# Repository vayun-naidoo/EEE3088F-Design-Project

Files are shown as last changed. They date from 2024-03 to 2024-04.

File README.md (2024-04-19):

**EEE3088F MICRO MOUSE DESIGN PROJECT**  
The project requires the construction of two submodules that interface with a micromouse robot. The robot is designed to complete a maze after finding the most optimal path to traverse.
The two submodules are for the **power** and **sensing** requirements of the micromouse. All design schematics and datasheets considered can be found in this repository.  

**POWER**  
The power submodule is required to distrubute the power from a 1S1P battery to the motors on the micromouse as well as power the other submodules such as the processor and the sensing apparatus. 
THe system is also required to monitor the battery's state of charge (SoC) through the processor's ADC.

**SENSING**  
The sensing subsystem is required to, at close range(+-5cm) produce a voltage to the micro controller. This voltage must be distinguishable from a further range output(+10cm). It is also required to not drain the battery of the micro mouse as it needs to traverse a maze for roughly 10 minutes.

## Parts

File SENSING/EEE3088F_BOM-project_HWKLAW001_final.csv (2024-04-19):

Comment | Designator | Footprint | LCSC
NPN | Q9 | SOT-23 | C139719
100 | R2 | R_0805_2012Metric | C17408
10k | R17,R20,R8 | R_0805_2012Metric | C17414
150 | R3 | R_0805_2012Metric | C17471
1k | R19,R22,R31 | R_0805_2012Metric | C17513
20 | R1,R10,R11,R12,R13,R14,R15,R5,R6,R7,R9 | R_0805_2012Metric | C17544
51 | R23 | R_0805_2012Metric | C17738
5k | R16,R18,R21,R24,R4 | R_0805_2012Metric | C27834
D_Photo | D2,D7,D8 | LED_D5.0mm_Horizontal_O1.27mm_Z3.0mm_IRBlack | C2900211
LD271 | D1,D10,D3,D4,D5,D6 | LED_SideEmitter_Rectangular_W4.5mm_H1.6mm | C57092
SJ_OPEN | JP17 | SolderJumper-2_P1.3mm_Open_RoundedPad1.0x1.5mm
SJ_OPEN | JP2 | SolderJumper-2_P1.3mm_Open_RoundedPad1.0x1.5mm
SJ_OPEN | JP5 | SolderJumper-2_P1.3mm_Open_RoundedPad1.0x1.5mm
SJ_OPEN | JP10 | SolderJumper-2_P1.3mm_Open_RoundedPad1.0x1.5mm
SJ_OPEN | JP6 | SolderJumper-2_P1.3mm_Open_RoundedPad1.0x1.5mm
SJ_OPEN | JP7 | SolderJumper-2_P1.3mm_Open_RoundedPad1.0x1.5mm
TestPoint | TP1 | TestPoint_Pad_1.5x1.5mm
TestPoint | TP4 | TestPoint_Pad_1.5x1.5mm
SJ_OPEN | JP16 | SolderJumper-2_P1.3mm_Open_RoundedPad1.0x1.5mm
SJ_OPEN | JP8 | SolderJumper-2_P1.3mm_Open_RoundedPad1.0x1.5mm
SJ_OPEN | JP9 | SolderJumper-2_P1.3mm_Open_RoundedPad1.0x1.5mm
Conn_01x28_Pin | J1 | PinSocket_2x14_P2.54mm_Vertical
SJ_OPEN | JP3 | SolderJumper-2_P1.3mm_Open_RoundedPad1.0x1.5mm
SJ_OPEN | JP24 | SolderJumper-2_P1.3mm_Open_RoundedPad1.0x1.5mm
SJ_OPEN | JP4 | SolderJumper-2_P1.3mm_Open_RoundedPad1.0x1.5mm
SJ_OPEN | JP1 | SolderJumper-2_P1.3mm_Open_RoundedPad1.0x1.5mm
SJ_OPEN | JP18 | SolderJumper-2_P1.3mm_Open_RoundedPad1.0x1.5mm
TestPoint | TP2 | TestPoint_Pad_1.5x1.5mm

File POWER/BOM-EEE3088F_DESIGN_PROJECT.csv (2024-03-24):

Comment | Designator | Footprint | LCSC
0.1uF | C1,C2 | C_0603_1608Metric | C14663
1.2k | R1 | R_0805_2012Metric | C17379
470 | R4 | R_0805_2012Metric | C17710
4.7uF | C3,C4 | C_0805_2012Metric | C1779
SW_SPDT | SW1 | SW_Lever_1P2T_NKK_GW12LxH | C1788490
LED | D1 | LED_0603_1608Metric | C2286
LEFT MOTOR | U1,U2 | WSON-8-1EP_2x2mm_P0.5mm_EP0.9x1.6mm | C39159
2k | R3 | R_0402_1005Metric | C4109
3k | R2 | R_0603_1608Metric | C4211
MCP73831-2-OT | U3 | SOT-23-5 | C424093

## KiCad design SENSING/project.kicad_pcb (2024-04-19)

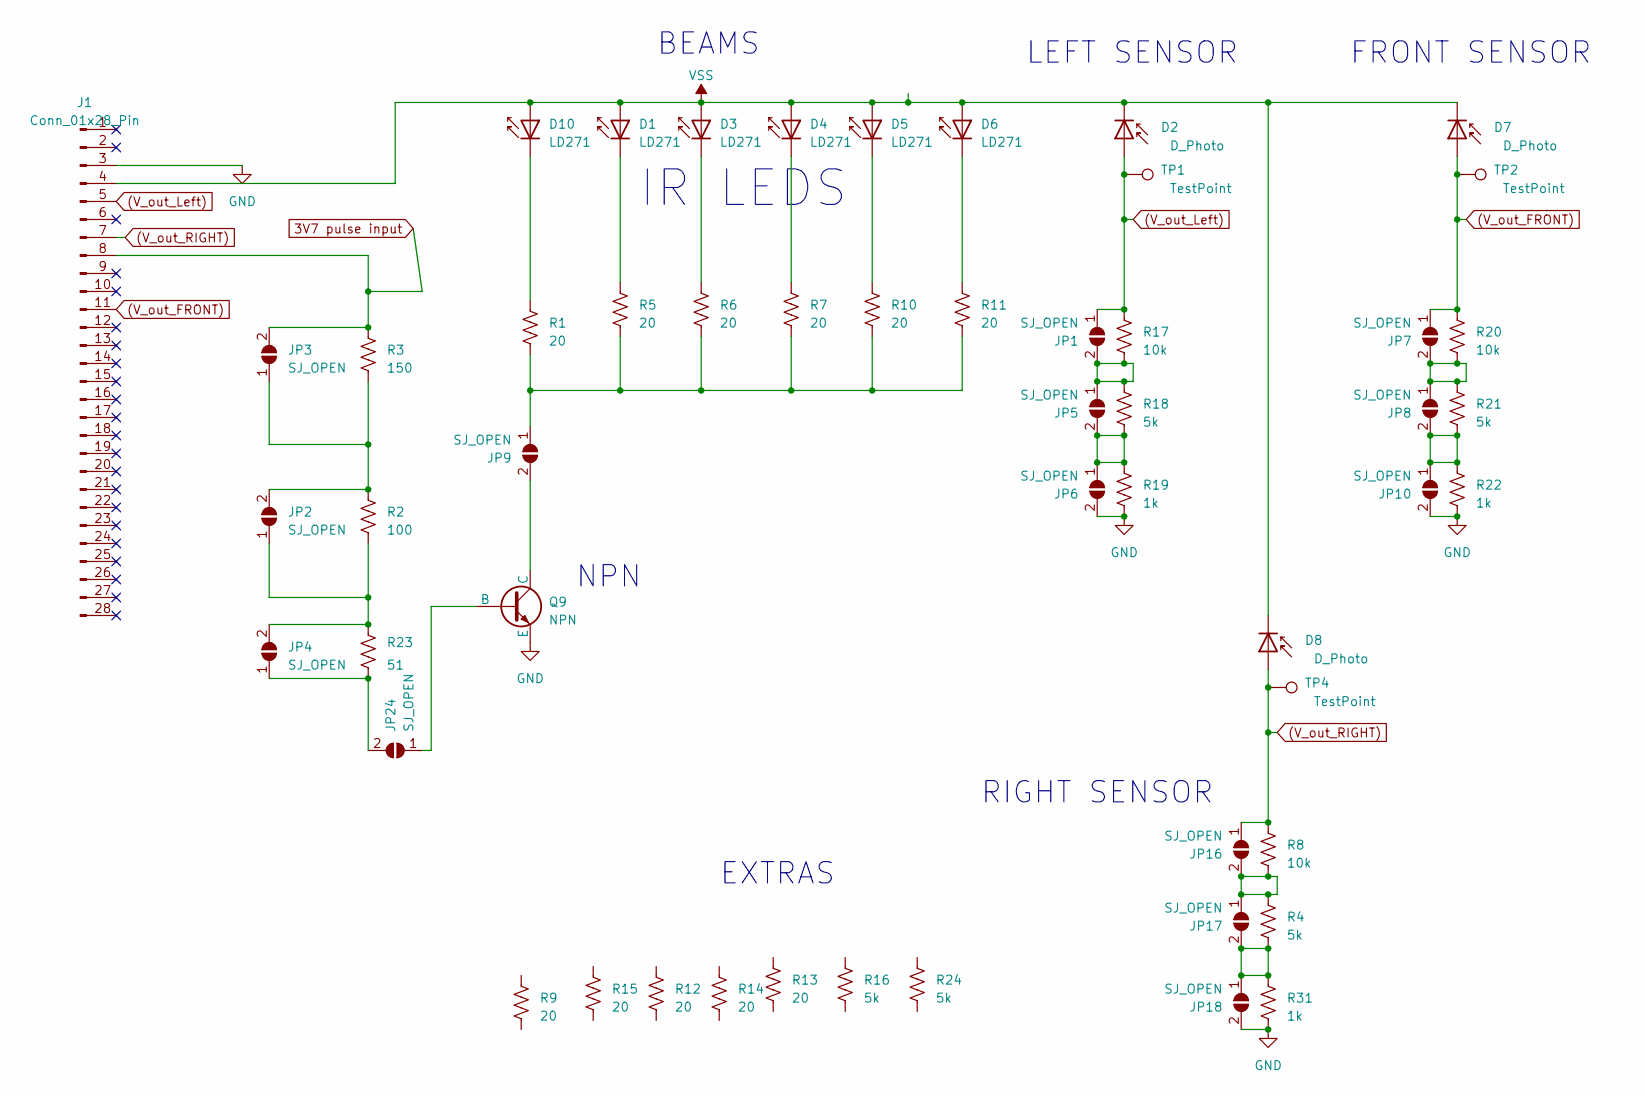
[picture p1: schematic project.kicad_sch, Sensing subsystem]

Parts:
D1, D3, D4, D5, D6, D10: LD271; LED_SideEmitter_Rectangular_W4.5mm_H1.6mm; LCSC C57092
D2, D7, D8: D_Photo; LED_D5.0mm_Horizontal_O1.27mm_Z3.0mm_IRBlack; LCSC C2900211
J1: Conn_01x28_Pin; PinSocket_2x14_P2.54mm_Vertical
JP1, JP2, JP3, JP4, JP5, JP6, JP7, JP8, JP9, JP10, JP16, JP17, JP18, JP24: SJ_OPEN; SolderJumper-2_P1.3mm_Open_RoundedPad1.0x1.5mm
Q9: NPN; SOT-23; LCSC C139719
R1, R5, R6, R7, R9, R10, R11, R12, R13, R14, R15: 20; R_0805_2012Metric; LCSC C17544
R2: 100; R_0805_2012Metric; LCSC C17408
R3: 150; R_0805_2012Metric; LCSC C17471
R4, R16, R18, R21, R24: 5k; R_0805_2012Metric; LCSC C27834
R8, R17, R20: 10k; R_0805_2012Metric; LCSC C17414
R19, R22, R31: 1k; R_0805_2012Metric; LCSC C17513
R23: 51; R_0805_2012Metric; LCSC C17738
TP1, TP2, TP4: TestPoint; TestPoint_Pad_1.5x1.5mm

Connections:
3V7 pulse input: J1.8, JP3.2 (B), R3.2
(V_out_FRONT): D7.2 (A), J1.11, JP7.1 (A), R20.1, TP2.1
(V_out_Left): D2.2 (A), J1.5, JP1.1 (A), R17.1, TP1.1
(V_out_RIGHT): D8.2 (A), J1.7, JP16.1 (A), R8.1, TP4.1
GND: J1.3, JP6.2 (B), JP10.2 (B), JP18.2 (B), Q9.3 (E), R19.2, R22.2, R31.2
unnamed: D1.1 (K), R5.2
unnamed: D3.1 (K), R6.2
unnamed: D4.1 (K), R7.2
unnamed: D5.1 (K), R10.2
unnamed: D6.1 (K), R11.2
unnamed: D10.1 (K), R1.2
unnamed: JP1.2 (B), JP5.1 (A), R17.2, R18.1
unnamed: JP2.1 (A), JP4.2 (B), R2.1, R23.2
unnamed: JP2.2 (B), JP3.1 (A), R2.2, R3.1
unnamed: JP5.2 (B), JP6.1 (A), R18.2, R19.1
unnamed: JP7.2 (B), JP8.1 (A), R20.2, R21.1
unnamed: JP9.1 (A), R1.1, R5.1, R6.1, R7.1, R10.1, R11.1
unnamed: JP9.2 (B), Q9.1 (C)
unnamed: JP8.2 (B), JP10.1 (A), R21.2, R22.1
unnamed: JP16.2 (B), JP17.1 (A), R4.1, R8.2
unnamed: JP17.2 (B), JP18.1 (A), R4.2, R31.1
unnamed: JP24.1 (A), Q9.2 (B)
unnamed: JP4.1 (A), JP24.2 (B), R23.1
VSS: D1.2 (A), D2.1 (K), D3.2 (A), D4.2 (A), D5.2 (A), D6.2 (A), D7.1 (K), D8.1 (K), D10.2 (A), J1.4

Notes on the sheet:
NPN
LEFT SENSOR
IR LEDS
EXTRAS
FRONT SENSOR
BEAMS
RIGHT SENSOR

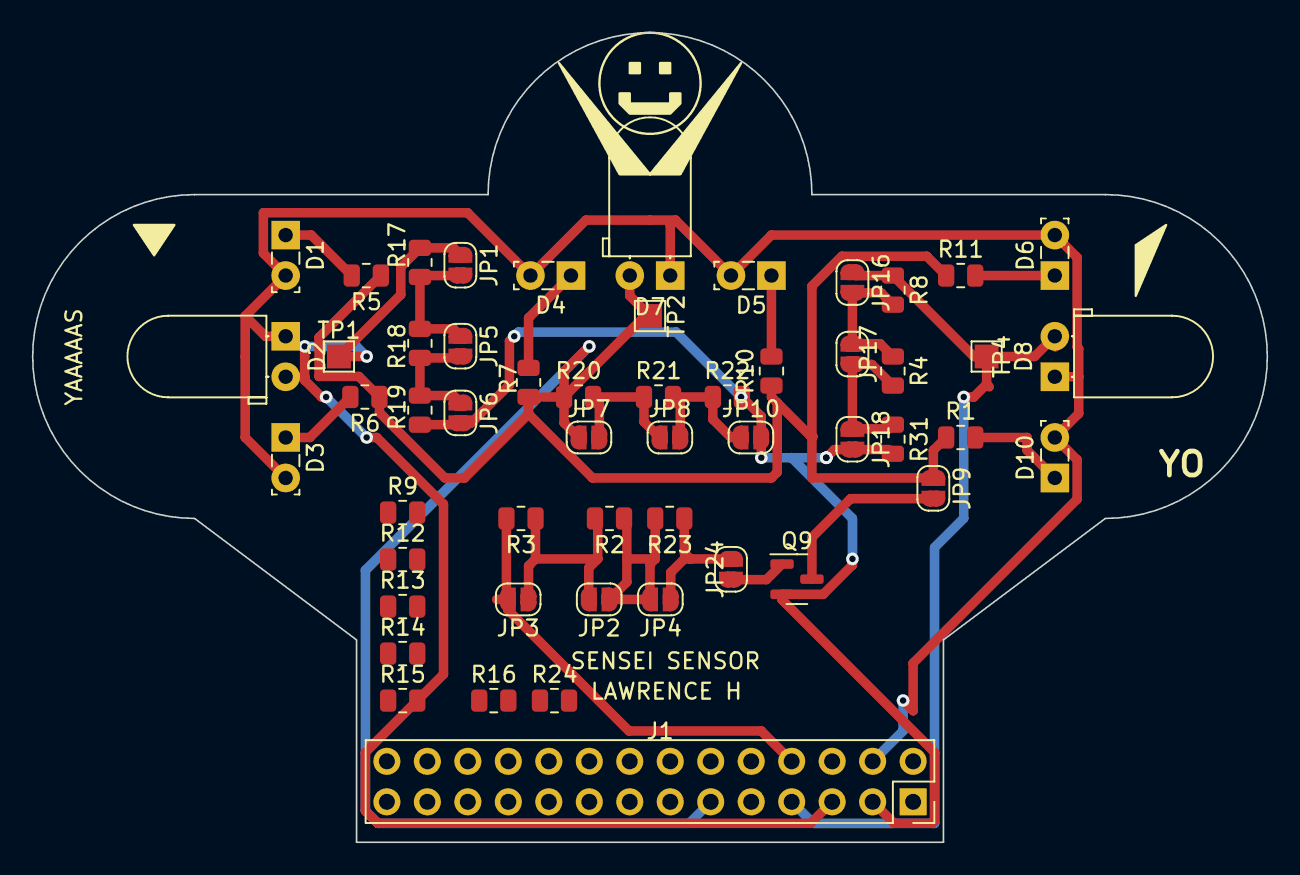
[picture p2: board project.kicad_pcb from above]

Board: 2 copper layers, 77.5 x 50.8 mm, 53 parts (0 on the bottom side), 24 nets.
